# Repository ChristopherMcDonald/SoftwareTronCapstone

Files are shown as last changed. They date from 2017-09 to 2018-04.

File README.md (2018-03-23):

# SmartServe
An Autonomous Table Tennis Trainer

## Team Members
- Christopher McDonald
- Harit Patel
- Janak Patel
- Jared Rayner
- Nisarg Patel
- Sam Hamel
- Sharon Platkin

## Context
This project is the final capstone project for the Team Member's Bachelor of Engineering degrees.

## Overview
SmartServe is an autonomous table tennis training system for table tennis players with various skill levels. SmartServe aids in diagnosing and improving a player's performance over time. The system trains table tennis players by shooting table tennis balls towards the player and detects successful returns from the player. The system can further adapt to the player's weaknesses and help them overcome it through further training. Importantly, SmartServe alleviates the problems of finding and working with a coach for players, as well as coaches trying to train multiple players simultaneously. The system will be deemed a success if the table tennis players and coaches, can enjoy and see a value added by using SmartServe.

The project started at the beginning of the Fall 2017 academic term and will conclude at the end of the Winter 2018 term. In addition, the core project team consists of final year Software and Mechatronics Engineering students who are enrolled in the MECHTRON 4TB6/SFWRENG 4G06 capstone project course.

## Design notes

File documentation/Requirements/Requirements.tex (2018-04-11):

\documentclass[11pt]{article} 
\usepackage{geometry}
\geometry{letterpaper}

\usepackage{graphicx}   
\usepackage{amssymb}
\usepackage{float}
\usepackage{tabularx}
\usepackage{framed}
\usepackage{hyperref}
\hypersetup{
    colorlinks,
    citecolor=black,
    filecolor=black,
    linkcolor=black,
    urlcolor=black
}
\usepackage{cleveref}
%\usepackage[autostyle]{csquotes}
\usepackage[english]{babel}
\usepackage[backend=biber,style=numeric,sorting=none]{biblatex}
\addbibresource{cites.bib}

\defbibheading{bibliography}[\refname]{}

\begin{document}

\begin{titlepage}
	\newcommand{\HRule}{\rule{\linewidth}{0.2mm}}
	\begin{center}
	\textsc{\LARGE McMaster University}\\[1.5cm]
	
	\textsc{\Large SmartServe}\\[0.5cm]
	\textsc{\large Software \& Mechatronics Capstone}\\[0.5cm] 

	\HRule\\[0.4cm]
		{\huge\bfseries Requirements Document}\\[0.4cm]
	\HRule\\[0.4cm]
	
	\begin{minipage}[t][][t]{0.5\textwidth}
		\begin{flushleft} \large
			\emph{Authors:}\\
			Christopher McDonald - \textit{001312456} \\
			Harit Patel - \textit{001317372}\\
			Janak Patel - \textit{001307060} \\
			Jared Rayner - \textit{001311702}\\
			Nisarg Patel - \textit{001322805} \\
			Sam Hamel - \textit{001321692} \\
			Sharon Platkin - \textit{001316625} \\
		\end{flushleft}
	\end{minipage}
	~
	\begin{minipage}[t][][t]{0.4\textwidth}
		\begin{flushright} \large
			\emph{Professor:} \\
			Dr. Alan Wassyng \\[0.4cm]
			\emph{Teaching Assistants:} \\
			Bennett Mackenzie \\ 
			Nicholas Annable \\ 
			Stephen Wynn-Williams \\ 
			Viktor Smirnov
		\end{flushright}
	\end{minipage}\\[2cm]
	
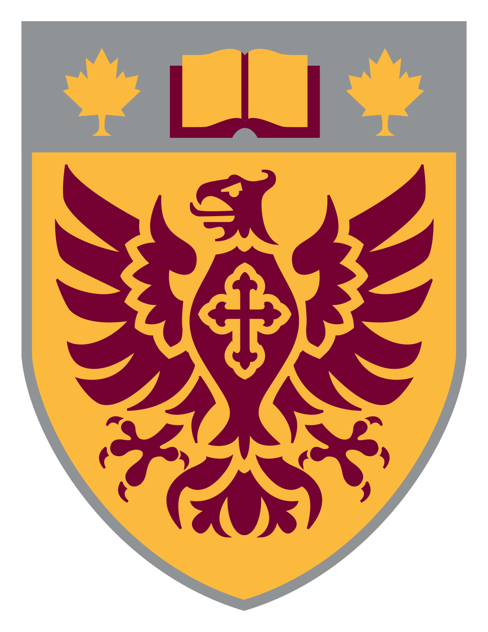
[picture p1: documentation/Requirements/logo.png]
	 \\
	{\large Last compiled on \today}
	\end{center}

\end{titlepage}

\tableofcontents
\listoffigures

\vfill
\begin{figure}[htbp]
   \centering
   \noindent\begin{tabularx}{\textwidth}{| >{\centering\arraybackslash}m{0.2\textwidth} | >{\centering\arraybackslash}m{0.2\textwidth} | >{\centering\arraybackslash}m{0.2\textwidth} | >{\centering\arraybackslash}m{0.285\textwidth} |}
   \hline 
   \textbf{Date} & \textbf{Revision} & \textbf{Comments} & \textbf{Author(s)} \\
   \hline
   10/06/2017 & 0 & Made Template, added sections and comments & Christopher McDonald \\ \hline
   10/13/2017 & 1 & Added Overview and reviewed & Christopher McDonald \& Sharon Platkin \\ \hline
   10/13/2017 & 2 & Reviewed and Corrected Project Drivers section & Nisarg Patel \\ \hline
   10/20/2017 & 3 & Functional Requirements & Christopher McDonald \& Sharon Platkin \\ 
\hline
   11/05/2017 & 4 & Final Revision and Review & Nisarg Patel 
  \& Christopher McDonald \\   \hline
   \end{tabularx}
   \caption{Revision History}
\end{figure}

\newpage

% TA Comments - Rev 1
%FIXED (see diagram in Appendix): What is a "4x4 grid"?
%FIXED (see accuracy added to fit crit for F2): Repeatability requirement on speed of ball? Angle of shooting mechanism or shot?
%FIXED (angular velocity is a function of speed by our design, and thus accuracy / repeatability would be the same added 5 degrees of error for degree): Add quantification of and a requirement on magnitude and repeatability of spin
%COMMENT by Janak: I think this requires a discussion. Magnitude of the spin is dependent on speed of the motor which might give us unrealistic spins at realistic speeds, will know with more testing. Going to need metrics for measuring spins also which could get challenging depending on how accurately we want to measure it.     
%FIXED (switched to 95): Detecting only 90% of returns may undermine the ability to train a person. Maybe aim for higher.
%COMMENT by Harit: Actually I thought 90% was quite reasonable to simply capture repeated mistakes and areas of improvement. Especially since SmartServe is catered to non-professional players
%COMMENY by Chris: fixed, good call ^
%COMMENT by Chris: yeah, I dunno. I just changed to appease him.
%IGNORED (will remove if it becomes necessary): Specific timeline isn't really needed for project overview. Might have to cut it in the future for extra space.
%FIXED (switched to 'Display'): Define ?Open Profile? from figure 8?
%??? (I don't know about this one, as per the Volere template cards it appears to be internal people, link here - http://www.volere.co.uk/pdf%20files/06%20Atomic%20Requirements.pdf): Originator of the requirements is not a specific team member, but rather of the defined stakeholders.
%COMMENT By Harit: I think he means the originator should be the stakeholder this requirement should be satisfied for. But I've never seen this before, should confirm with Alan. If change is needed, in most case it will be the player or the coach.
%COMMENT by Chris: good with asking Alan,
%FIXED (updated description): The system must be able to support 1000 users? - 1000 players? 1 player and 999 trainers? Make it less ambiguous.
%FIXED (removed requirement, did NOT update identifiers): The software for the system will execute on Linux, Windows and MacOS operating systems? - I thought the system was self contained, and as such it would be used with whatever embedded OS of your choosing. This seems to be more of a requirement for a standalone software package, not a self-contained system.
%IGNORED (I can defend it :P politics can be within customer organization, team's organization or country politicts, link here - https://www.utdallas.edu/~chung/SYSM6309/NFR-18-4-on-1.pdf): Requirement P1. How is this a political requirement? Seems to be a straightforward
%COMMENT by Harit: HAHA good shit!
%COMMENT by Janak: Requirement ID for Political Requirements and Performance requirements will both have a "P" suffix. Do the Req IDs have to be unique? 
%IGNORED (see above): Don?t try to dig for requirements, if you have no political requirements, put none. In fact, political requirements by itself is not a concept, not in context of engineering.

% NOTES: we will not be adjusting / refragging Requirement identifiers

\section{Introduction}
\subsection{Project Overview}
SmartServe is an autonomous table tennis training system for table tennis players with various skill levels. SmartServe aids in diagnosing and improving a player's performance over time. The system trains table tennis players by shooting table tennis balls towards the player and detects successful returns from the player. The system can further adapt to the player's weaknesses and help them overcome it through further training. Importantly, SmartServe alleviates the problems of finding and working with a coach for players, as well as coaches trying to train multiple players simultaneously. The system will be deemed a success if the table tennis players and coaches can enjoy and see value in using SmartServe.\\\\
The project started at the beginning of the Fall 2017 academic term and will conclude at the end of the Winter 2018 term. In addition, the core project team consists of final year Software and Mechatronics Engineering students who are enrolled in the MECHTRON 4TB6/SFWRENG 4G06 capstone project course.
\subsection{Naming Conventions and Terminology}
\label{sec:definitions}
The following terms and definitions will be used throughout this document:
\begin{itemize}
\item \textbf{System}: encompasses both the hardware and software parts of SmartServe
\item \textbf{Shooting Mechanism}: refers to the part of the system that shoots the table tennis balls towards the user side (player)
\item \textbf{Team}: all team members of the core capstone project, as noted in the list of Authors
\item \textbf{User Side}: the side of the table where the user (player) is standing
\item \textbf{System Side}: the side of the table where the electromechanical system is placed; it is the opposite side of the User Side
\item \textbf{ACID}: a database transaction which is atomic, consistent, isolated and durable
\item \textbf{FPS}: frames per second
\item \textbf{GUI}: graphical user interface
\item \textbf{Pitch}: rotation along the y-axis; this rotation angle primarily dictates the range of the ball from the net to the edge of the table on the user side
\item \textbf{Yaw}: rotation along the z-axis; this rotation angle primarily dictates the panning functionality of the shooting mechanism from the right side to the left side of the table
\item \textbf{Roll}: rotation along the x-axis
\end{itemize}
\begin{figure}[H]
   \centering
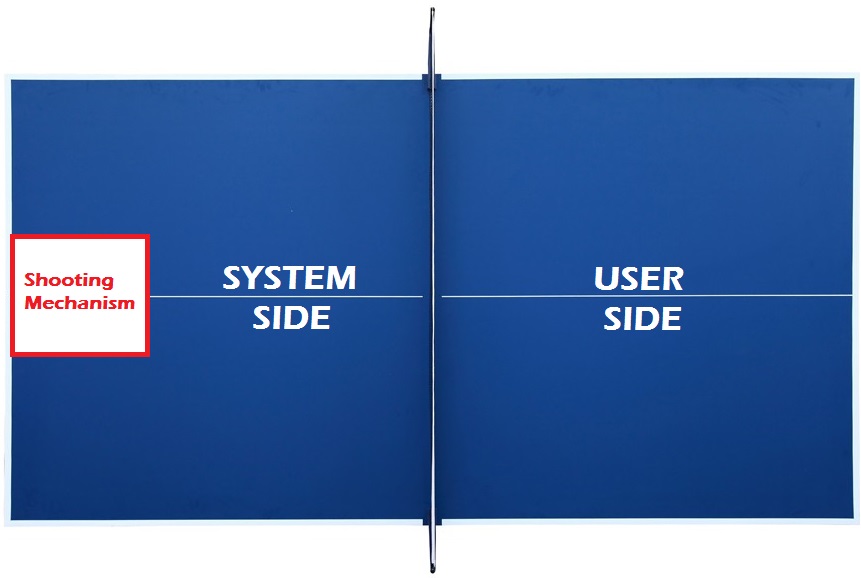
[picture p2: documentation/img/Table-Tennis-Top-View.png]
    %requires the graphicx package
   \caption{Top View of the Tennis Table}
   \label{fig:table-tennis-top-view}
\end{figure}
\begin{figure}[H]
   \centering
    %requires the graphicx package
   \caption{Pitch, Yaw and Roll Illustration}
   \label{fig:pitch_yaw_roll_diagram}
\end{figure}

\subsection{Relevant Facts \& Assumptions}
According to the International Table Tennis Federation (ITTF), the regulation table size is as follows: 2.74m long, 1.525m wide and 0.76m high off the ground. The table must be a uniformly dark colour with a 2cm-thick white line along the edge of the table, as well one running parallel to the 2.74m side in the middle of the table. The net in the middle of the table must be 15.25cm vertically high from the table~\autocite{ITTF}. A 3D representation of the table setup is illustrate in \Cref{fig:table-tennis-dim}. The size of a regulated table tennis ball is 40mm in diameter~\autocite{ITTF}. For this project, the \hyperref[sec:definitions]{team} will be using 40mm balls due to the ITTF regulation.\\
\begin{figure}[htbp]
   \centering
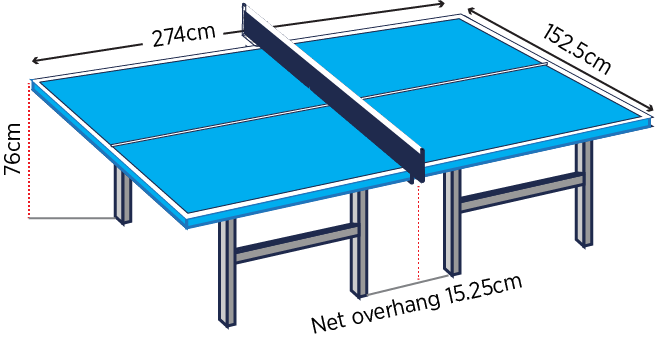
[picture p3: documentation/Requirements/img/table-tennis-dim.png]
    % requires the graphicx package
   \caption{3D Tennis Table with Dimensions}
   \label{fig:table-tennis-dim}
   % The Laws of Table Tennis. ITTF Handbook 2016. www.ittf.com/ittf_handbook/ittf_hb.html
\end{figure} \\
During gameplay, a valid serve must hit the \hyperref[sec:definitions]{server side} first, and then bounce once on the other player's side before being returned. After that is done, a valid return would be when the ball is hit by a player, after bouncing exactly once on their side, and bounces at least one time on the opposing player's side. If a serve touches the net and lands on the opposing player's side, it is a \textit{let}. No points are allocated and the turn must be re-served. These rules change during \textit{Double's Gameplay} but will not be considered for this project as only one user will be supported during operation.

\section{Project Drivers}
\subsection{Purpose}
% should include problem, lack of current solutions and ideal solution
When a player wants to improve their table tennis game, a typical solution is to hire a coach. However, this does not come without its challenges. Some of these challenges include scheduling, focusing on particular shots and receiving in-depth statistical feedback. Our proposed solution will consist of a shooting mechanism, a way to identify successful returns and a system to recommend different shots. Throughout the training session, the \hyperref[sec:definitions]{system} will provide the user with crucial feedback on the quality of their game. The system will consist of a electromechanical system to shoot the ball and a computer vision system to track the ball's location during flight. A server will also be added to store data, provide diagnostics and recommend shots given the user's past performance.
\subsection{Key Stakeholders}
\subsubsection{Client}
The client for this project comprises of the core development \hyperref[sec:definitions]{team} as both the idea and the project execution will be undertaken by the \hyperref[sec:definitions]{team}. It is also important to note that the project adviser, Dr. Alan Wassyng, as well as his teaching assistants will be involved in the project execution in order to provide guidance and critical feedback to the project \hyperref[sec:definitions]{team}.
\subsubsection{Users}
The primary users of this project are table tennis players. Our proposed \hyperref[sec:definitions]{system} will adapt to various playing styles and levels, and hence segmenting those players down further is not required at this stage. These users are more likely to play competitively, but could also play recreationally with friends or within a club focused around the sport. \\\\
The secondary users of this project are table tennis coaches. Although this \hyperref[sec:definitions]{system} could replace a coach, a coach could find value in using this system to aid in training and assisting multiple players at one time. The system will provide analytics on players performance that can be very useful when training someone over a long period of time.
\subsubsection{Faculty}
The Department of Computing and Software at McMaster University is also a key stakeholder for this project. The development \hyperref[sec:definitions]{team} are students of this department and would thus represent it through the work they perform. This project is also the amalgamation of the knowledge attained by the \hyperref[sec:definitions]{team} over their undergraduate degrees. If the project is unsuccessful, the department loses the opportunity to showcase it for future students and donors.

\section{Project Scope}
\subsection{The Scope of the Work and the Product}
In order to make the project feasible within the time constraint imposed on the \hyperref[sec:definitions]{team}, it will need to be scoped accordingly. One way we are scoping the project is by limiting the types of shots the \hyperref[sec:definitions]{system} can take. A return by the system would first contact the table on the \hyperref[sec:definitions]{\textit{User side}} where a serve would first contact the table on the \hyperref[sec:definitions]{\textit{System side}}. We are limiting the system to only preform returns. The system will make no attempt at returning any shots from the user. \\\\
After the user has returned a shot from the system, the system will not make any attempts to return a shot that is likely to be returned given the user's returns. This is to give the system the ability to focus on a particular type of shot the user is the least proficient at returning. The characteristics of the shot following any return will be determined by the system's mode and the proficiency of the player if available.
\subsubsection{Individual Product Use Cases}
The actors which will be interacting with the \hyperref[sec:definitions]{system} are the \textbf{trainee}, the \textbf{coach} and the \textbf{system administrator}. It is not necessary for a coach to be present, but they will have the ability to use the system alongside the trainee. See \Cref{fig:usecase} for the use case diagram. The following list contains all primary use cases:
\begin{itemize}
\item A trainee enters their login information
\item If the login information is correct, a trainee opens their training session on the \hyperref[sec:definitions]{system}
\item A trainee begins the training session
\item A trainee selects a training mode
\item A trainee pauses the training session
\item When the system is paused, a trainee ends the training session
\item A trainee inspects their performance
\end{itemize}
The following are secondary use cases:
\begin{itemize}
\item A coach inspects trainee's performance
\item A coach adjusts training parameters during training session
\item A system administrator calibrates the system for new tables of a non-regulation size
\end{itemize}

\begin{figure}[H]
   \centering
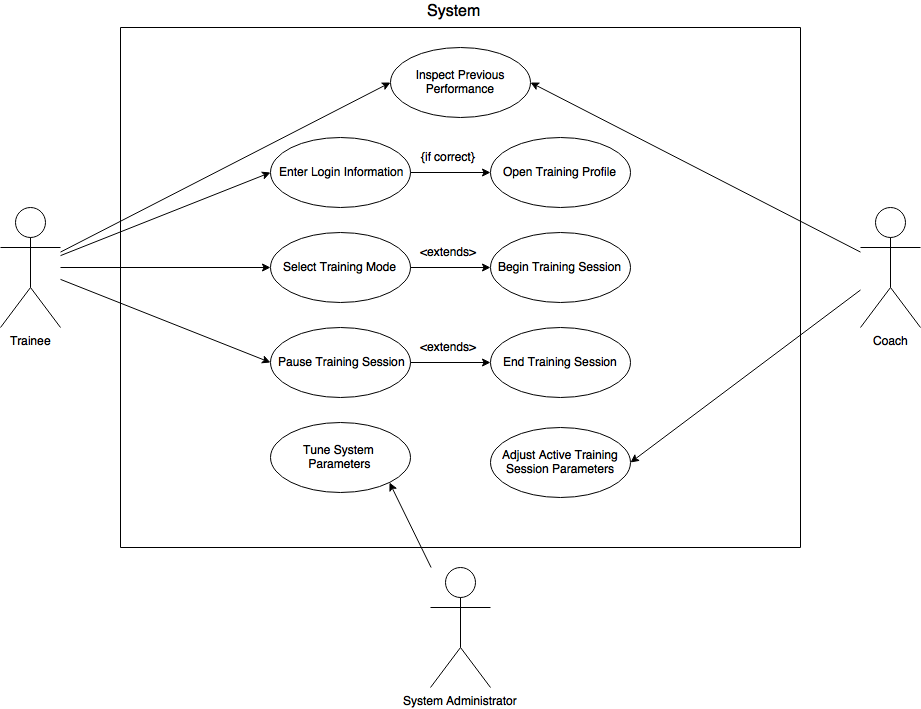
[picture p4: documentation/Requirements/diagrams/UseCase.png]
   
   \caption{Use Case Diagram}
   \label{fig:usecase}
\end{figure}
\subsection{Mandated Constraints}
The first constraint placed on the project is time. The deliverable and presentation dates have been set, concluding with the presentations booked for April 27, 2018. Therefore, the \hyperref[sec:definitions]{team} must successfully submit all of the deliverables and complete the project by April 27th, 2018. Additionally, a budget constraint of \$750 on the Bill of Materials (BOM) for the final product is also enforced.
\subsection{Undesired Behaviour} 
The shooting mechanism should not start, pause or end a session without the user triggering the event. The \hyperref[sec:definitions]{system} must also refrain from shooting the ball outside the speed and angle ranges specified. Furthermore, the system should not attempt to shoot balls when it runs out of balls. \\\\

\subsection{Variables}
\begin{figure}[H]
   \centering
   \noindent\begin{tabularx}{\textwidth}{| >{\centering\arraybackslash}m{0.2\textwidth} | >{\centering\arraybackslash}m{0.2\textwidth} | >{\centering\arraybackslash}m{0.2\textwidth} | >{\centering\arraybackslash}m{0.285\textwidth} |}
   \hline 
   \textbf{Variable Name} & \textbf{Type} & \textbf{Value} & \textbf{Description} \\ \hline
   \textit{Table Length} & Final & 274cm & The longest edge of the table tennis table \\ \hline
   \textit{Table Width} & Final & 152.5cm & Perpendicular to the \textit{Table Length} \\ \hline
   \textit{Ball Diameter} & Final & 40mm & Diameter of the ball used by the system \\ \hline
   \textit{Ball Location} & Monitored & X, Y and Z cm & Relative to the center of the table on its surface \\ \hline
   \textit{Shooting Mechanism Position} & Monitored & $\alpha_p$ and $\alpha_y$ degrees & Pitch and Yaw of the shooting mechanism \\ \hline
   \textit{User Performance} & Monitored & $\lambda_1$, $\lambda_2$, ... $\lambda_n$ & Return rates for n different shots from the user \\ \hline
 
\end{tabularx}
\caption{List of Variables}
\end{figure}

\subsection{Context Diagram}
\begin{figure}[H]
   \centering
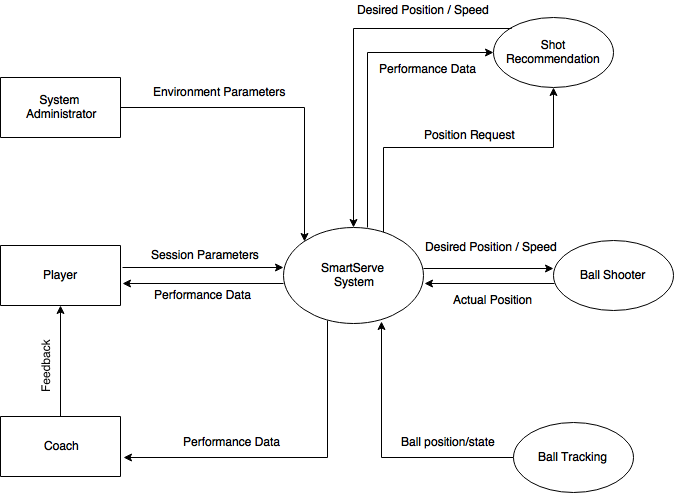
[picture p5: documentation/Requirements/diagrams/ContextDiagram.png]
   
   \caption{Context Diagram}
   \label{fig:ContextDiagram}
\end{figure}

\section{Functional Decomposition Diagram}
\begin{figure}[H]
   \centering
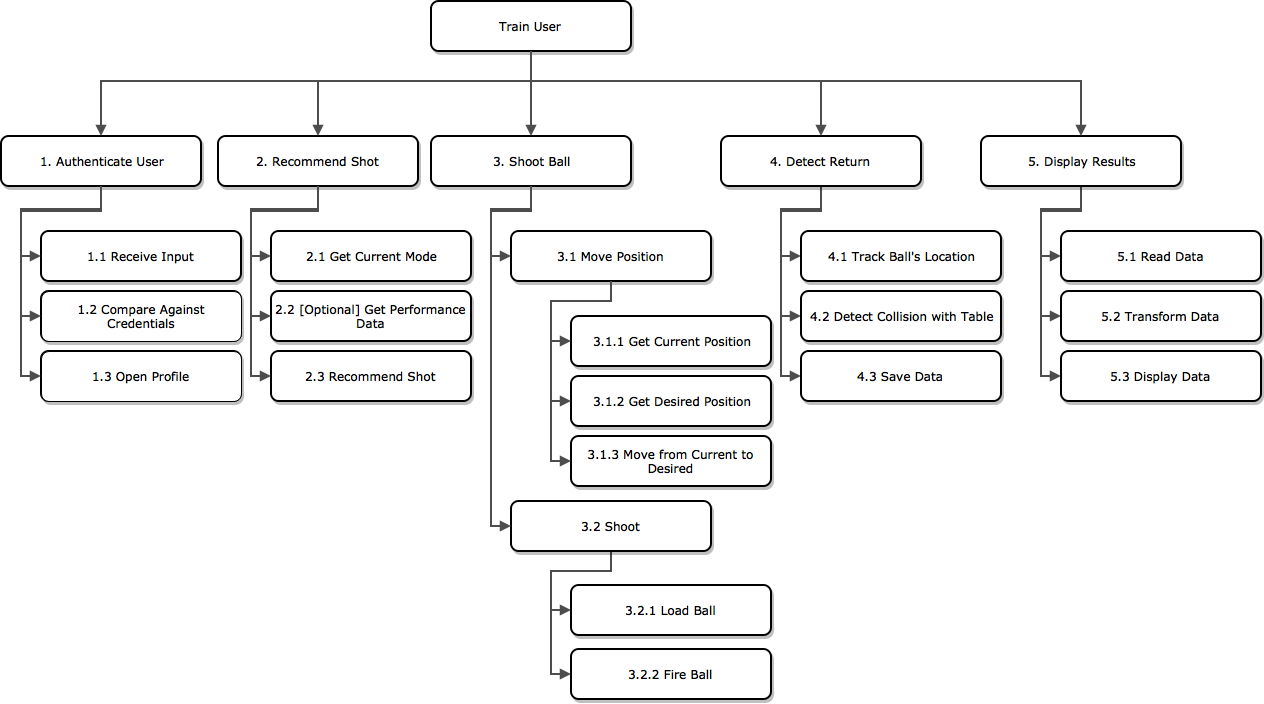
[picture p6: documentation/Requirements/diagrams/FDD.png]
   
   \caption{Functional Decomposition Diagram}
   \label{fig:fdd}
\end{figure}

\section{Functional Requirements}

\begin{framed}
	\noindent\textbf{Requirement ID}: F1 \hfill \textbf{Requirement Type}: F \hfill\\\\
	\noindent\textbf{Description}: The \hyperref[sec:definitions]{shooting mechanism} shoots the table tennis ball towards the \hyperref[sec:definitions]{user side} at various locations \\
	\textbf{Rationale}: Provides variability in the shots made towards the user \\
	\textbf{Fit Criterion}: The \hyperref[sec:definitions]{shooting mechanism} can hit a specified section of a 4x4 grid with an accuracy of 75\%, an example of this grid can be found in Figure \ref{fig:zones}\\\\
	\textbf{Originator}: Sharon Platkin \\\\
	\textbf{Priority}: High \hfill \\
	\noindent\textbf{History}: Created Oct. 20, 2017
\end{framed}

\begin{framed}
	\noindent\textbf{Requirement ID}: F2 \hfill \textbf{Requirement Type}: F \hfill\\\\
	\noindent\textbf{Description}: The \hyperref[sec:definitions]{shooting mechanism} shoots the table tennis ball towards the \hyperref[sec:definitions]{user side} at various speeds \\
	\textbf{Rationale}: Provides variability in the shots made towards the user \\
	\textbf{Fit Criterion}: Since the fastest recorded speed of a table tennis ball is 31.25 m/s, the system should be able to match at least half this speed~\autocite{thoughtco}. Specifically, the \hyperref[sec:definitions]{shooting mechanism} must shoot at speeds ranging from 10 to 15 m/s at discrete increments of 0.5 within 0.1 m/s of error \\\\
	\textbf{Originator}: Sharon Platkin \\\\
	\textbf{Priority}: High \hfill \\
	\noindent\textbf{History}: Created Oct. 20, 2017
\end{framed}

\begin{framed}
	\noindent\textbf{Requirement ID}: F3 \hfill \textbf{Requirement Type}: F \hfill\\\\
	\noindent\textbf{Description}: The \hyperref[sec:definitions]{shooting mechanism} shoots the table tennis ball towards the \hyperref[sec:definitions]{user side} at various degrees of \hyperref[sec:definitions]{Yaw} \\
	\textbf{Rationale}: Provides variability in the shots made towards the user \\
	\textbf{Fit Criterion}: The \hyperref[sec:definitions]{shooting mechanism} can shoot the ball at -30 to 30 degrees relative to the longest bisection of the table at discrete increments of 1 degree to have complete coverage of the \hyperref[sec:definitions]{User Side}, see \Cref{fig:calc} for calculations \\\\
	\textbf{Originator}: Sharon Platkin \\\\
	\textbf{Priority}: High \hfill \\
	\noindent\textbf{History}: Created Oct. 20, 2017
\end{framed}

\begin{framed}
	\noindent\textbf{Requirement ID}: F4 \hfill \textbf{Requirement Type}: F \hfill\\\\
	\noindent\textbf{Description}: The \hyperref[sec:definitions]{shooting mechanism} shoots the table tennis ball towards the \hyperref[sec:definitions]{user side} of the table with various degrees of roll \\
	\textbf{Rationale}: Provides variability in the shots made towards the user \\
	\textbf{Fit Criterion}: The \hyperref[sec:definitions]{shooting mechanism} can spin the ball at 0 to 360 degrees in discrete increments of 45 degrees on the longitudinal axis with 5 degrees of error\\\\ % longitudinal - refers to lengthwise as opposed to across
	\textbf{Originator}: Sharon Platkin \\\\
	\textbf{Priority}: High \hfill \\
	\noindent\textbf{History}: Created Oct. 20, 2017
\end{framed}

\begin{framed}
	\noindent\textbf{Requirement ID}: F5 \hfill \textbf{Requirement Type}: F \hfill\\\\
	\noindent\textbf{Description}: The \hyperref[sec:definitions]{system} can detect a successful return by the user \\
	\textbf{Rationale}: Allows quantitative information to be collected on the user's performance \\
	\textbf{Fit Criterion}: The system must detect 90\% of all successful returns made by the user\\\\
	\textbf{Originator}: Sharon Platkin \\\\
	\textbf{Priority}: High \hfill \\
	\noindent\textbf{History}: Created Oct. 20, 2017
\end{framed}

\begin{framed}
	\noindent\textbf{Requirement ID}: F6 \hfill \textbf{Requirement Type}: F \hfill\\\\
	\noindent\textbf{Description}: The \hyperref[sec:definitions]{system} saves the details for each shot taken by the shooting mechanism \\
	\textbf{Rationale}: Serves the purpose of saving the state and resuming sessions over time \\
	\textbf{Fit Criterion}: After each shot is returned, an \hyperref[sec:definitions]{ACID} save transaction is performed \\\\
	\textbf{Originator}: Christopher McDonald \\\\
	\textbf{Priority}: Medium \hfill \\
	\noindent\textbf{History}: Created Oct. 20, 2017
\end{framed}

\begin{framed}
	\noindent\textbf{Requirement ID}: F7 \hfill \textbf{Requirement Type}: F \hfill\\\\
	\noindent\textbf{Description}: The \hyperref[sec:definitions]{system} can load a previously saved state \\
	\textbf{Rationale}: This will allow the user to continue a training session at different times, even if the system is powered down \\
	\textbf{Fit Criterion}: \\\\
	\textbf{Originator}: Christopher McDonald \\\\
	\textbf{Priority}: Medium \hfill \\
	\noindent\textbf{History}: Created Oct. 20, 2017
\end{framed}

\begin{framed}
	\noindent\textbf{Requirement ID}: F8 \hfill \textbf{Requirement Type}: F \hfill\\\\
	\noindent\textbf{Description}: The \hyperref[sec:definitions]{system} allows the creation of a new user \\
	\textbf{Rationale}: This allows many users to use one system \\
	\textbf{Fit Criterion}: A user must be able to be created only if the user does not already exist in the system \\\\
	\textbf{Originator}: Christopher McDonald \\\\
	\textbf{Priority}: Medium \hfill \\
	\noindent\textbf{History}: Created Oct. 20, 2017
\end{framed}

\begin{framed}
	\noindent\textbf{Requirement ID}: F9 \hfill \textbf{Requirement Type}: F \hfill\\\\
	\noindent\textbf{Description}: The \hyperref[sec:definitions]{system} must authenticate users \\
	\textbf{Rationale}: This will ensure a user can access their profile and restrict other users from accessing their profile \\
	\textbf{Fit Criterion}: No user can access another user's profile and will have access to their own 99\% of the time \\\\
	\textbf{Originator}: Christopher McDonald \\\\
	\textbf{Priority}: High \hfill \\
	\noindent\textbf{History}: Created Oct. 20, 2017
\end{framed}

\begin{framed}
	\noindent\textbf{Requirement ID}: F10 \hfill \textbf{Requirement Type}: F \hfill\\\\
	\noindent\textbf{Description}: The \hyperref[sec:definitions]{system} can pause the shooting mechanism \\
	\textbf{Rationale}: A user may need to attend other matters during training or get real-time feedback from the system \\
	\textbf{Fit Criterion}: After instantiating the pause process, the system shoots at most 1 more ball(s) \\\\
	\textbf{Originator}: Christopher McDonald \\\\
	\textbf{Priority}: High \hfill \\
	\noindent\textbf{History}: Created Oct. 20, 2017
\end{framed}

\begin{framed}
	\noindent\textbf{Requirement ID}: F11 \hfill \textbf{Requirement Type}: F \hfill\\\\
	\noindent\textbf{Description}: The \hyperref[sec:definitions]{system} can end the training session \\
	\textbf{Rationale}: This will be used when a user is done training \\
	\textbf{Fit Criterion}: N/A \\\\
	\textbf{Originator}: Christopher McDonald \\\\
	\textbf{Priority}: High \hfill \\
	\noindent\textbf{History}: Created Oct. 20, 2017
\end{framed}

\begin{framed}
	\noindent\textbf{Requirement ID}: F12 \hfill \textbf{Requirement Type}: F \hfill\\\\
	\noindent\textbf{Description}: The \hyperref[sec:definitions]{system} can resume a training session from a paused state \\
	\textbf{Rationale}: N/A \\
	\textbf{Fit Criterion}: N/A \\\\
	\textbf{Originator}: Christopher McDonald \\\\
	\textbf{Priority}: High \hfill \\
	\noindent\textbf{History}: Created Oct. 20, 2017
\end{framed}

\begin{framed}
	\noindent\textbf{Requirement ID}: F13 \hfill \textbf{Requirement Type}: F \hfill\\\\
	\noindent\textbf{Description}: The \hyperref[sec:definitions]{system} can display the user's performance over a custom time range \\
	\textbf{Rationale}: This will aid the user in diagnosing their ability to play table tennis \\
	\textbf{Fit Criterion}: N/A\\\\
	\textbf{Originator}: Christopher McDonald \\\\
	\textbf{Priority}: High \hfill \\
	\noindent\textbf{History}: Created Oct. 20, 2017
\end{framed}

\begin{framed}
	\noindent\textbf{Requirement ID}: F14 \hfill \textbf{Requirement Type}: F \hfill\\\\
	\noindent\textbf{Description}: The \hyperref[sec:definitions]{system} has a \textbf{training} mode \\
	\textbf{Rationale}: This mode will focus on playing to the user's weaknesses more so than others \\
	\textbf{Fit Criterion}: After 100 pseudo-randomly distributed shots, the system will begin to distribute the shots differently. By ordering each class of shot from the least to most returned, the first 15\%, the next 35\% and the last half will all receive an equal share of shots. \\\\
	\textbf{Originator}: Christopher McDonald \\\\
	\textbf{Priority}: High \hfill \\
	\noindent\textbf{History}: Created Oct. 20, 2017
\end{framed}

\begin{framed}
	\noindent\textbf{Requirement ID}: F15 \hfill \textbf{Requirement Type}: F \hfill\\\\
	\noindent\textbf{Description}: The \hyperref[sec:definitions]{system} has a \textbf{one-shot} mode \\
	\textbf{Rationale}: This mode will focus on playing to one particular class of shot, as described by the user \\
	\textbf{Fit Criterion}: For all shots performed in this mode, 90\% must be classified as the same as the one entered \\\\
	\textbf{Originator}: Christopher McDonald \\\\
	\textbf{Priority}: Medium \hfill \\
	\noindent\textbf{History}: Created Oct. 20, 2017
\end{framed}

\begin{framed}
	\noindent\textbf{Requirement ID}: F16 \hfill \textbf{Requirement Type}: F \hfill\\\\
	\noindent\textbf{Description}: The \hyperref[sec:definitions]{system} allows a user to adjust training parameters during a session which is active or paused \\
	\textbf{Rationale}: A coach may want to push a player to train in a particular area \\
	\textbf{Fit Criterion}:  \\\\
	\textbf{Originator}: Christopher McDonald \\\\
	\textbf{Priority}: Low \hfill \\
	\noindent\textbf{History}: Created Oct. 20, 2017
\end{framed}

\begin{framed}
	\noindent\textbf{Requirement ID}: F17 \hfill \textbf{Requirement Type}: F \hfill\\\\
	\noindent\textbf{Description}: The \hyperref[sec:definitions]{system} can be calibrated for the size of the table \\
	\textbf{Rationale}: As performed by a system administrator, it should be usable for all non-regulation table sizes \\
	\textbf{Fit Criterion}: The system follows all documented requirements \\\\
	\textbf{Originator}: Christopher McDonald \\\\
	\textbf{Priority}: High \hfill \\
	\noindent\textbf{History}: Created Oct. 20, 2017
\end{framed}

\begin{framed}
	\noindent\textbf{Requirement ID}: F18 \hfill \textbf{Requirement Type}: F \hfill\\\\
	\noindent\textbf{Description}: The \hyperref[sec:definitions]{shooting mechanism} will shoot a ball once the previous has been returned to the \hyperref[sec:definitions]{system side} or 1.5 seconds after the previous shot, whichever happens first\\
	\textbf{Rationale}: This will ensure the system is reasonably fast and keeps the user engaged, as well as compensates for more experienced players. \\
	\textbf{Fit Criterion}: N/A \\\\
	\textbf{Originator}: Christopher McDonald \\\\
	\textbf{Priority}: High \hfill \\
	\noindent\textbf{History}: Created Oct. 20, 2017
\end{framed}

\section{Non-Functional Requirements}

\subsection{Look and Feel Requirements}
\begin{framed}
	\noindent\textbf{Requirement ID}: LF1 \hfill\\\\
	\noindent\textbf{Description}: The \hyperref[sec:definitions]{system} will have a minimalist design that is easy to navigate through \\
	\textbf{Rationale}: A minimalistic design will help with user discover all the options and settings of the system  \\
	\textbf{Fit Criterion}: The user must be able to navigate to any feature from the profile page in at most two steps.  \\\\
	\textbf{Originator}: Sam Hamel \\\\
	\textbf{Priority}: Medium \hfill \\
	\noindent\textbf{History}: Created Oct. 27, 2017
\end{framed}

\subsection{Usability and Humanity Requirements}
\begin{framed}
	\noindent\textbf{Requirement ID}: UH1 \hfill\\\\
	\noindent\textbf{Description}: The \hyperref[sec:definitions]{system} must be intuitive to use \\
	\textbf{Rationale}: As the system is adding onto an existing process, it should not cause strain for the user to operate \\
	\textbf{Fit Criterion}: The user must be able to create a user in less than 30 seconds. The user must be able to initiate \textit{one-shot} mode in less than 2 minutes from opening their profile.  \\\\
	\textbf{Originator}: Christopher McDonald \\\\
	\textbf{Priority}: High \hfill \\
	\noindent\textbf{History}: Created Oct. 20, 2017
\end{framed}

\begin{framed}
	\noindent\textbf{Requirement ID}: UH2 \hfill\\\\
	\noindent\textbf{Description}: The \hyperref[sec:definitions]{system} will operate using the English language \\
	\textbf{Rationale}: Some of the Development \hyperref[sec:definitions]{team} only speaks English \\
	\textbf{Fit Criterion}: All outputs generated by the system will be in English  \\\\
	\textbf{Originator}: Sharon Platkin \\\\
	\textbf{Priority}: High \hfill \\
	\noindent\textbf{History}: Created Oct. 27, 2017
\end{framed}

\subsection{Performance Requirements}

\begin{framed}
	\noindent\textbf{Requirement ID}: P1 \hfill\\\\
	\noindent\textbf{Description}: The response time of feedback for user input must be less than or equal to 100ms \\
	\textbf{Rationale}: 100ms is the approximate maximum amount of time for the user to perceive the system as reacting instantaneously~\autocite{response}. Users should feel that all inputs have been registered by the system\\
	\textbf{Fit Criterion}: Any click inputs that generate feedback must do so in at most 100ms.  \\\\
	\textbf{Originator}: Sam Hamel \\\\
	\textbf{Priority}: High \hfill \\
	\noindent\textbf{History}: Created Oct. 27, 2017
\end{framed}

\begin{framed}
	\noindent\textbf{Requirement ID}: P2 \hfill\\\\
	\noindent\textbf{Description}: The system must include all but the previous 3 shots made toward the user  \\
	\textbf{Rationale}: This will keep the performance measures relatively up to date for relevant and up-to-date feedback \\
	\textbf{Fit Criterion}: Any results by any return from the player must be displayed on the \hyperref[sec:definitions]{GUI} (graphical user interface) before the player returns 3 more shots \\\\
	\textbf{Originator}: Sam Hamel \\\\
	\textbf{Priority}: High \hfill \\
	\noindent\textbf{History}: Created Oct. 27, 2017
\end{framed}

\begin{framed}
	\noindent\textbf{Requirement ID}: P4 \hfill\\\\
	\noindent\textbf{Description}: The \hyperref[sec:definitions]{system} must be able to support a total of 1000 users, consisting of players and coaches \\
	\textbf{Rationale}: If the system is used by a company, they will have a large amount of users using the system\\
	\textbf{Fit Criterion}: The system can store up to a thousand user profiles and their accompanying performance history data \\\\
	\textbf{Originator}: Sam Hamel \\\\
	\textbf{Priority}: Medium \hfill \\
	\noindent\textbf{History}: Created Oct. 27, 2017
\end{framed}

\begin{framed}
	\noindent\textbf{Requirement ID}: P5 \\\\
	\noindent\textbf{Description}: The \hyperref[sec:definitions]{system} will be able to support only one user playing at any given time \\
	\textbf{Rationale}: The system will not be able to differentiate between player returns if they were more than one user playing at the same time \\
	\textbf{Fit Criterion}: The system will work as expected for one player playing 99\% of the time \\\\
	\textbf{Originator}: Sam Hamel \\\\
	\textbf{Priority}: High \hfill \\
	\noindent\textbf{History}: Created Oct. 27, 2017
\end{framed}

\subsection{Operational and Environmental Requirements}

\begin{framed}
	\noindent\textbf{Requirement ID}: OE2 \\\\
	\noindent\textbf{Description}: The \hyperref[sec:definitions]{system} will be functional in indoor settings with bright florescent lighting in the room \\
	\textbf{Originator}: Sam Hamel \\\\
	\textbf{Priority}: High \hfill \\
	\noindent\textbf{History}: Created Oct. 27, 2017
\end{framed}

\subsection{Maintainability and Support Requirements}

\begin{framed}
	\noindent\textbf{Requirement ID}: MS2 \\\\
	\noindent\textbf{Description}: The \hyperref[sec:definitions]{system} should be able to add new metrics to analyze performance\\
	\textbf{Rationale}: More efficient and appropriate methods may be found in order to analyze player performance\\
	\textbf{Fit Criterion}: The system will be able to add new performance metrics and analysis methods so long as no changes need to be made to the hardware\\\\
	\textbf{Originator}: Sam Hamel \\\\
	\textbf{Priority}: High \hfill \\
	\noindent\textbf{History}: Created Oct. 27, 2017
\end{framed}

\subsection{Security Requirements}
\begin{framed}
	\noindent\textbf{Requirement ID}: S1 \hfill\\\\
	\noindent\textbf{Description}: The \hyperref[sec:definitions]{system} must hash all passwords for user profiles \\
	\textbf{Rationale}: If the system is compromised, no person should be able to read user's passwords in plain text. \\
	\textbf{Fit Criterion}: The system uses a hashing algorithm currently supported by NIST, the National Institute of Standards and Technology.\\\\
	\textbf{Originator}: Christopher McDonald \\\\
	\textbf{Priority}: High \hfill \\
	\noindent\textbf{History}: Created Oct. 20, 2017
\end{framed}

\begin{framed}
	\noindent\textbf{Requirement ID}: S2 \hfill\\\\
	\noindent\textbf{Description}: The \hyperref[sec:definitions]{system} must encrypt all performance data for each user \\
	\textbf{Rationale}: If the system is compromised, no person should be able to exploit an opponent's weaker aspects \\
	\textbf{Fit Criterion}: The system uses an encrypting algorithm currently supported by NIST, the National Institute of Standards and Technology.\\\\
	\textbf{Originator}: Christopher McDonald \\\\
	\textbf{Priority}: Low \hfill \\
	\noindent\textbf{History}: Created Oct. 20, 2017
\end{framed}

\subsection{Political Requirements}
\begin{framed}
	\noindent\textbf{Requirement ID}: P1\\\\
	\noindent\textbf{Description}: The \hyperref[sec:definitions]{system} must allow full read access for coaches \\
	\textbf{Rationale}: If a coach purchases this system, they should be able to analyze all players information for training purposes \\
	\textbf{Fit Criterion}: \\\\
	\textbf{Originator}: Christopher McDonald \\\\
	\textbf{Priority}: Medium \hfill \\
	\noindent\textbf{History}: Created Oct. 20, 2017
\end{framed}
\subsection{Legal \& Compliance Requirements}
\begin{framed}
	\noindent\textbf{Requirement ID}: LC1 \hfill\\\\
	\noindent\textbf{Description}: The \hyperref[sec:definitions]{system} must comply and operate for all ITTF rules and regulations \\
	\textbf{Rationale}: ITTF mandates the acceptance of all table tennis equipment and the system should work with these to be used by professional players \\
	\textbf{Fit Criterion}: The system must work for any 2 tables and nets which the ITTF has accepted \\\\
	\textbf{Originator}: Christopher McDonald \\\\
	\textbf{Priority}: High \hfill \\
	\noindent\textbf{History}: Created Oct. 20, 2017
\end{framed}
\subsection{Health and Safety Requirements}
\begin{framed}
	\noindent\textbf{Requirement ID}: HS1 \hfill\\\\
	\noindent\textbf{Description}: The \hyperref[sec:definitions]{shooting mechanism} will always hit the table at least once  \\
	\textbf{Rationale}: This will give the user more time and context to react to the shot \\
	\textbf{Fit Criterion}: The system imposes limits for speed and pitch of the shot \\\\
	\textbf{Originator}: Christopher McDonald \\\\
	\textbf{Priority}: High \hfill \\
	\noindent\textbf{History}: Created Oct. 20, 2017
\end{framed}

\begin{framed}
	\noindent\textbf{Requirement ID}: HS2 \hfill\\\\
	\noindent\textbf{Description}: The \hyperref[sec:definitions]{shooting mechanism} will not shoot the ball faster than 22 m/s \\
	\textbf{Rationale}: This is 70\% of one of the world's fastest shots taken in table tennis and is unlikely to be of any practical use\\
	\textbf{Fit Criterion}: The system will constrain the speed of its shooting mechanism \\\\
	\textbf{Originator}: Christopher McDonald \\\\
	\textbf{Priority}: High \hfill \\
	\noindent\textbf{History}: Created Oct. 20, 2017
\end{framed}

\begin{framed}
	\noindent\textbf{Requirement ID}: HS3 \hfill\\\\
	\noindent\textbf{Description}: The \hyperref[sec:definitions]{system} should have no exposed electronic wiring or components \\
	\textbf{Rationale}: This will protect the user from electric shocks and the system from damage \\
	\textbf{Fit Criterion}: Only by disassembling the system should wiring and components be exposed \\\\
	\textbf{Originator}: Christopher McDonald \\\\
	\textbf{Priority}: High \hfill \\
	\noindent\textbf{History}: Created Oct. 28, 2017
\end{framed}

\begin{framed}
	\noindent\textbf{Requirement ID}: HS4 \hfill\\\\
	\noindent\textbf{Description}: The \hyperref[sec:definitions]{system} will carry warnings around moving parts  \\
	\textbf{Rationale}: Moving parts can expose users to risk of pinching extremities \\
	\textbf{Fit Criterion}: Warning signs are displayed at every point of risk \\\\
	\textbf{Originator}: Christopher McDonald \\\\
	\textbf{Priority}: High \hfill \\
	\noindent\textbf{History}: Created Oct. 28, 2017
\end{framed}

\begin{framed}
	\noindent\textbf{Requirement ID}: HS5 \hfill\\\\
	\noindent\textbf{Description}: The \hyperref[sec:definitions]{system} will have a button to cease all power to the system \\
	\textbf{Rationale}: In the case of dangerous operation, the system must be able to be powered off manually \\
	\textbf{Fit Criterion}: One button will shut down system and is labeled as such \\\\
	\textbf{Originator}: Christopher McDonald \\\\
	\textbf{Priority}: High \hfill \\
	\noindent\textbf{History}: Created Oct. 28, 2017
\end{framed}

\section{Project Issues}
\subsection{Open Issues}
Due to the nature of the project, all aspects of it must operate proficiently in order for it to be successful. For example, one potential issue would arise if no spin must be applied to the ball. Without detailing how the system works, the team considers this to be difficult without hardware that has no error in operation. \\\\
Some players may be able to hit the ball much faster than the solution we build to capture successful returns. For example, if some optical sensor is used it must be fast enough to capture the ball at the point of contact, or very close to it, in order to accurately determine if it did hit the table. \\\\
Between shots of the \hyperref[sec:definitions]{system}, it must determine where the next shot will be, get into the necessary position and shoot the ball. For some cases, the shot determination could take longer than usual or the distance between initial and final state could be far. This could jeopardize the system's ability to meet requirement F18.
\subsection{Off-the-Shelf Solutions}
For the second issue noted in the above section, a high speed camera could be used but would exceed the budget constraint placed on this project. For example, a GoPro HERO5 camera can film at 120fps but costs \$490~\autocite{amazon-gopro}.
Additionally, a camera which can film up to 500fps costs as much as \$999.99~\autocite{all-sport}.
These would far constrain our budget, but would solve the issue should it arise. An alternative could be mat embedded with sensors, omitting all optical sensor requirements. A mat which is roughly one-quarter the size of what we would need to cover one side of table costs \$119.99, which includes a wireless pager and any markup costs done by the manufacturer. A total estimate for our materials can be estimated to be \$150.00.\\\\
For the third issue, faster motors could be used to make the shooting mechanism move faster. However, these also must fit in the budget and will be adjusted accordingly to do so.
\subsection{New Problems}
As of \today, no new problems exist.
\subsection{Risks}
The largest and only risk to note is potentially going over budget. This is mainly with respect to the proficiency of the sensors and motors used as it is typically positively correlated with price. 
\subsection{User Documentation \& Training}
The user should be informed on the following items in order to use the system effectively:
\begin{itemize}
\item Available training modes and their purpose
\item How to read performance charts and data
\item Load table tennis balls into the correct location
\item Ensure system is positioned correctly
\end{itemize}
\section{Likely Changes}
As noted in the Project Goals document, many of the anticipated changes include enhanced accuracy of some requirements. These include the following:
\begin{itemize}
\item F1 will be changed to a 8x8 grid and then a 16x16 grid
\item Adding a \textbf{random} shooting mode
\item Adding variable heights for the shooting mechanism
\item Adding the ability to track the ball throughout its travel across the table
\end{itemize}
\section{Appendix}
\begin{figure}[H]
\centering

\caption{Valid Range of Shot Calculation}
\label{fig:calc}
\end{figure}

\begin{figure}[H]
   \centering
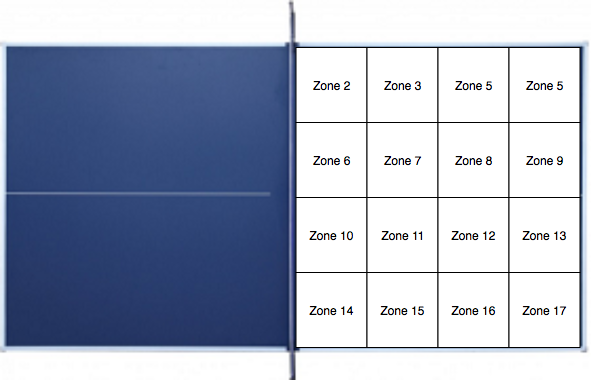
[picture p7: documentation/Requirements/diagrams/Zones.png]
    % requires the graphicx package
   \caption{Table Tennis Table with 4x4 Grid Zones}
   \label{fig:zones}
\end{figure}
\section{References}
\printbibliography
\end{document}

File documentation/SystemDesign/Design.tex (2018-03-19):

\documentclass[11pt]{article}
\usepackage{geometry}
\geometry{letterpaper}

\usepackage{graphicx}
\usepackage{amssymb}
\usepackage{float}
\usepackage{tabularx}
\usepackage{multicol}
\usepackage{rotating}
\usepackage{hyperref}
\hypersetup{
    colorlinks,
    citecolor=black,
    filecolor=blue,
    linkcolor=black,
    urlcolor=black
}

% TODOs:
% ask Nick about lines in Seq Diagram, ask Nick about need 3D model, ask Nick about entering project goals
% switch to cleveref

\begin{document}

\begin{titlepage}
	\newcommand{\HRule}{\rule{\linewidth}{0.2mm}}
	\begin{center}
	\textsc{\LARGE McMaster University}\\[1.5cm]

	\textsc{\Large SmartServe}\\[0.5cm]
	\textsc{\large Software \& Mechatronics Capstone}\\[0.5cm]

	\HRule\\[0.4cm]
		{\huge\bfseries High Level System Design}\\[0.4cm]
	\HRule\\[0.4cm]

	\begin{minipage}[t][][t]{0.5\textwidth}
		\begin{flushleft} \large
			\emph{Authors:}\\
			Christopher McDonald - \textit{001312456} \\
			Harit Patel - \textit{001317372}\\
			Janak Patel - \textit{001307060} \\
			Jared Rayner - \textit{001311702}\\
			Nisarg Patel - \textit{001322805} \\
			Sam Hamel - \textit{001321692} \\
			Sharon Platkin - \textit{001316625} \\
		\end{flushleft}
	\end{minipage}
	~
	\begin{minipage}[t][][t]{0.4\textwidth}
		\begin{flushright} \large
			\emph{Professor:} \\
			Dr. Alan Wassyng \\[0.4cm]
			\emph{Teaching Assistants:} \\
			Bennett Mackenzie \\
			Nicholas Annable \\
			Stephen Wynn-Williams \\
			Viktor Smirnov
		\end{flushright}
	\end{minipage}\\[2cm]

	 \\
	{\large Last compiled on \today}
	\end{center}

\end{titlepage}

\tableofcontents
\listoffigures

\vfill
\begin{figure}[H]
   \centering
   \noindent\begin{tabularx}{\textwidth}{| >{\centering\arraybackslash}m{0.2\textwidth} | >{\centering\arraybackslash}m{0.2\textwidth} | >{\centering\arraybackslash}m{0.2\textwidth} | >{\centering\arraybackslash}m{0.285\textwidth} |}
   \hline
   \textbf{Date} & \textbf{Revision} & \textbf{Comments} & \textbf{Author(s)} \\ \hline
   Dec 1, 2017 & 1.0 & Main content done for all sections & Christopher McDonald \\ \hline
   Dec 13, 2017 & 1.1 & Corrected Document Overview & Nisarg Patel \\ \hline
   Dec 14, 2017 & 1.2 & Refined Project Scope \& System Description (Section 2) & Nisarg Patel \\ \hline
   Dec 17, 2017 & 1.3 & Added CRC card intro and reviewed & Christopher McDonald \\ \hline
   Dec 21, 2017 & 1.4 & Edited entire document & Sharon Platkin \\ \hline
   Dec 21, 2017 & 1.5 & Added Arduino Diagrams and Shooter Information & Nisarg Patel \\ \hline	
   Mar 9, 2018 & 2.0 & Added Likely / Unlikely Changes and Assumptions, Removed Shot Optimizer & Christopher McDonald \\ \hline	
   Mar 9, 2018 & 2.1 & Added motor specifications & Janak Patel \\ \hline	
   Mar 10, 2018 & 2.2 & Added details on CV and SR, fixed Start Sequence Diagram & Christopher McDonald \\ \hline
   Mar 10, 2018 & 2.3 & Fixed CRC cards for changes to requirements & Christopher McDonald \\ \hline
   Mar 18, 2018 & 2.4 & Converted to overall design, added in low level / component details & Christopher McDonald \\ \hline
   \end{tabularx}
   \caption{Revision History}
\end{figure}
\newpage
\section{Introduction}
\subsection{Project Overview}
SmartServe is an autonomous table tennis training system for table tennis players with various skill levels. SmartServe aids in diagnosing and improving a player's performance over time. The system trains table tennis players by shooting table tennis balls towards the player and detects successful returns from the player. The system can further adapt to the player's weaknesses and help them overcome it through further training. Importantly, SmartServe alleviates the problems of finding and working with a coach for players, as well as coaches trying to train multiple players simultaneously. The system will be deemed a success if the table tennis players and coaches can enjoy and see some value added by using SmartServe.\\\\
The project started at the beginning of the Fall 2017 academic term and will conclude at the end of the Winter 2018 term. In addition, the core project team consists of final year Software and Mechatronics Engineering students who are enrolled in the MECHTRON 4TB6/SFWRENG 4G06 capstone project course.
\subsection{Document Overview}
The purpose of this document is to provide an overview of the system design which meets the system requirements as specified in the \href{run:../Requirements/Requirements.pdf}{Requirements Document}. The system will be decomposed into subsystems, where each has responsibilities and is designed to fulfill certain requirements. The subsystems will have their intended input, expected output and description of how the module will be used. In further documentation, each will be designed in a way which is abstracted from this document's perspective. The expected use cases will also be detailed to understand the expectations of the user and how each subsystem interacts with one another. A more detailed view of this including timing as a factor will be detailed in the Sequence Diagram section. \\ \\ % TODO LINK EVERYTHING
For each subsystem, its purpose will be defined with respect to the overall system. After doing so, detailed input and output parameters will be defined. How each subsystem is architected is out of scope for this document and will be defined in further documentation. \\ \\

\subsection{Naming Conventions and Terminology}
\label{sec:definitions}
The following terms and definitions will be used throughout this document:
\begin{itemize}
% Alphabetical order is highly preferred as it eases user navigation
\item \textbf{ACID}: a database transaction which is atomic, consistent, isolated and durable
\item \textbf{CV}: computer vision
\item \textbf{FPS}: frames per second
\item \textbf{FSM}: finite state machine, shows transitions between states
\item \textbf{GUI}: graphical user interface
\item \textbf{IPO}: input process output
\item \textbf{Pitch}: rotation along the y-axis; this rotation angle primarily dictates the range of the ball from the net to the edge of the table on the user side
\item \textbf{Roll}: rotation along the x-axis
\item \textbf{Shooting Mechanism}: refers to the part of the system that shoots the table tennis balls towards the user side (player) Please refer to Figure \ref{fig:table-tennis-top-view} for visual illustration
\item \textbf{System}: encompasses both the hardware and software parts of SmartServe
\item \textbf{System Side}: the side of the table where the electromechanical system is placed; it is the opposite side of the User Side Please refer to Figure \ref{fig:table-tennis-top-view} for visual illustration
\item \textbf{TCP:} transmission control protocol
\item \textbf{Team}: all team members of the core capstone project, as noted in the list of Authors
\item \textbf{User Side}: the side of the table where the user (player) is standing
\item \textbf{Yaw}: rotation along the z-axis; this rotation angle primarily dictates the panning functionality of the shooting mechanism from the right side to the left side of the table
\end{itemize}

\begin{figure}[H]
   \centering
    %requires the graphicx package
   \caption{Top View of the Tennis Table}
   \label{fig:table-tennis-top-view}
\end{figure}
\subsection{Project Scope}
The system will only attempt to shoot balls from the shooting mechanism straight towards the user side. Notably, the system will not attempt to return any shots from the user. After the user has returned a shot, the Computer Vision (CV) subsystem will be utilized to determine if the user's shot lands on the table or not. Additionally, the characteristics of the shot following any return will be determined by the system's mode and the proficiency of the player if available.
\subsection{Assumptions}
This design assumes the user supplies a functioning webcam, a capable computer to run the software and can connect to the SmartServe system via USB. The computer should have proficient computing power, as the CV subsystem will suffer in proficiency as a result. It is also assumed the use cases described here cover all interactions the user will attempt to have with the system. We assume the user has a ITTF-approved table, an orange table tennis ball and a paddle to use.
\section{System Description}
\subsection{System Architecture}
The system will follow a service-oriented architecture. This means that a central subsystem will interface with several services that serve a single purpose. Some subsystems will be simply told what needs to be done and others will be asked for some return value. This is done to implement separation of concerns where one subsystem doesn't know everything about the system and only what is necessary to satisfy their requirements. It also allows for easy increments of versioning, where one subsystem can be used as long as it is functional and easily swapped out for a newer version with extra features or increased performance. Moreover, this system has heavy timing constraints and an unpredictable environment so some actions must be taken in absence of a service's response. For example, the computer vision may take longer to track a ball depending on its trajectory where the system must shoot another ball in order to keep the user engaged.

\subsection{Subsystems}
The system will be broken down into subsystems with the following purposes: 
\begin{itemize}
\item \textbf{SmartServe}: general management of subsystems
\item \textbf{Computer Vision}:  detection of returns
\item \textbf{Shooting Mechanism}:  shooting the ball toward the user
\item \textbf{Shot Recommendation}: provides best shot
\item \textbf{Data Storage}: storing the data
\item \textbf{Shooting Model}: modelling the shot's trajectory
\item \textbf{User Interface}: taking input from the user and showing output
\end{itemize}
The diagram for this breakdown can be found in Figure \ref{fig:sub}.
\begin{figure}[H]
   \centering
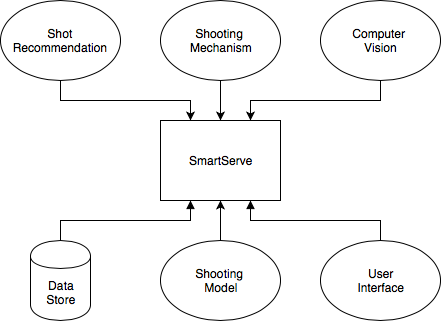
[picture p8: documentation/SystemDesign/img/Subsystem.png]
    % requires the graphicx package
   \caption{Subsystem Breakdown}
   \label{fig:sub}
\end{figure}
\subsection{Use Cases}
The diagram including all use cases can be found in Figure \ref{fig:usecase}. The user-instantiated ones will be described in detail below.
\begin{figure}[H]
   \centering
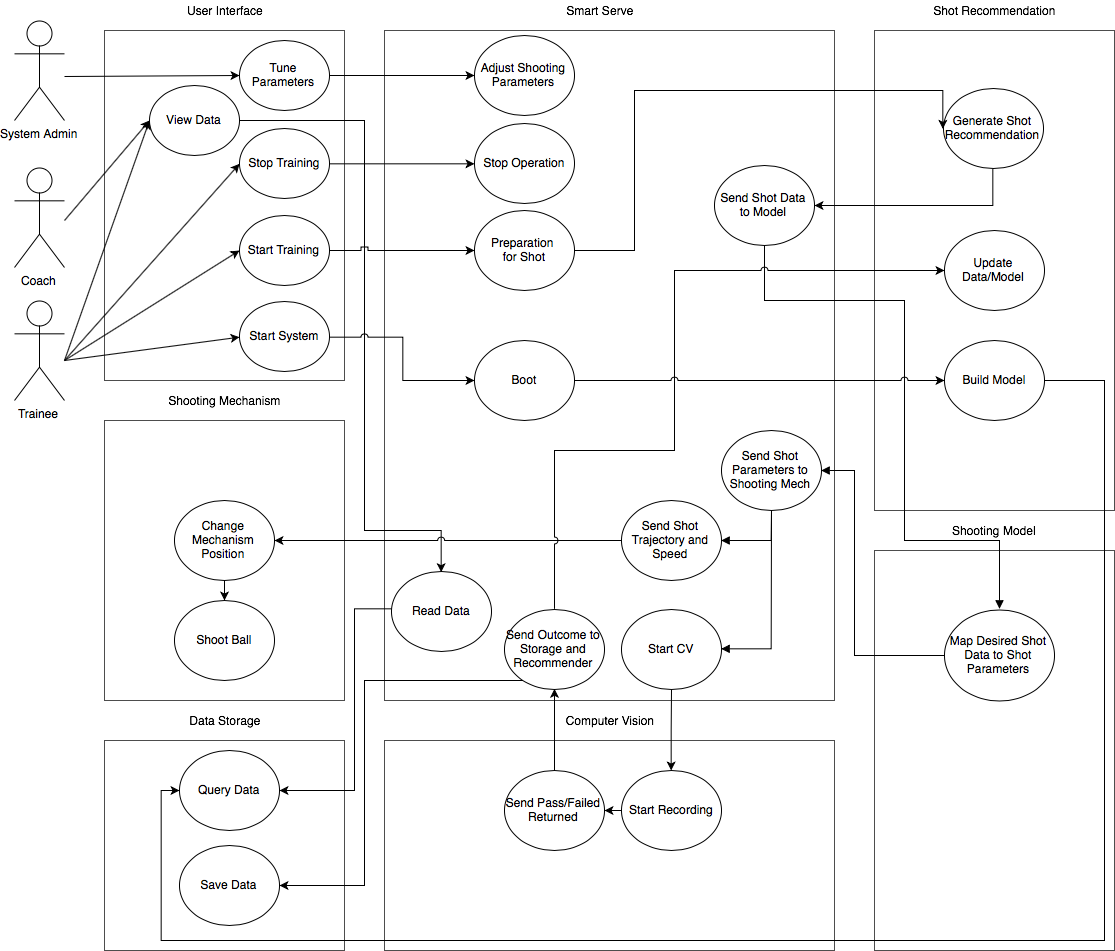
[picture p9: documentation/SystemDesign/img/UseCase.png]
    % requires the graphicx package
   \caption{Use Case Diagram}
   \label{fig:usecase}
\end{figure}
\subsubsection{Start Training}
The user interface will have ways to allow the user to start this action which makes the Smart Serve subsystem prepare for a shot to shoot towards the user. To do this, it needs to request a shot to use from the Shot Recommendation subsystem. The shot includes the following parameters: desired location on the table, the speed of the shot and the angular velocity of the ball. The Smart Serve subsystem can then use the Shooting Model to translate this information into pitch, yaw and angular velocity to shoot the ball so it matches the desired shot. After doing so, it will instruct the shooting mechanism to shoot the ball with the appropriate parameters and start the CV subsystem to begin tracking for a successful return. Only until the CV subsystem returns the pass or failed return data, can it update the Data Storage and Shot Recommendation subsystems with this new information. The former will store the result and the data for the shot together, where the latter will update the model used to generate shot recommendations. Upon completion, it can begin preparing for a new shot.
\begin{figure}[H]
   \centering
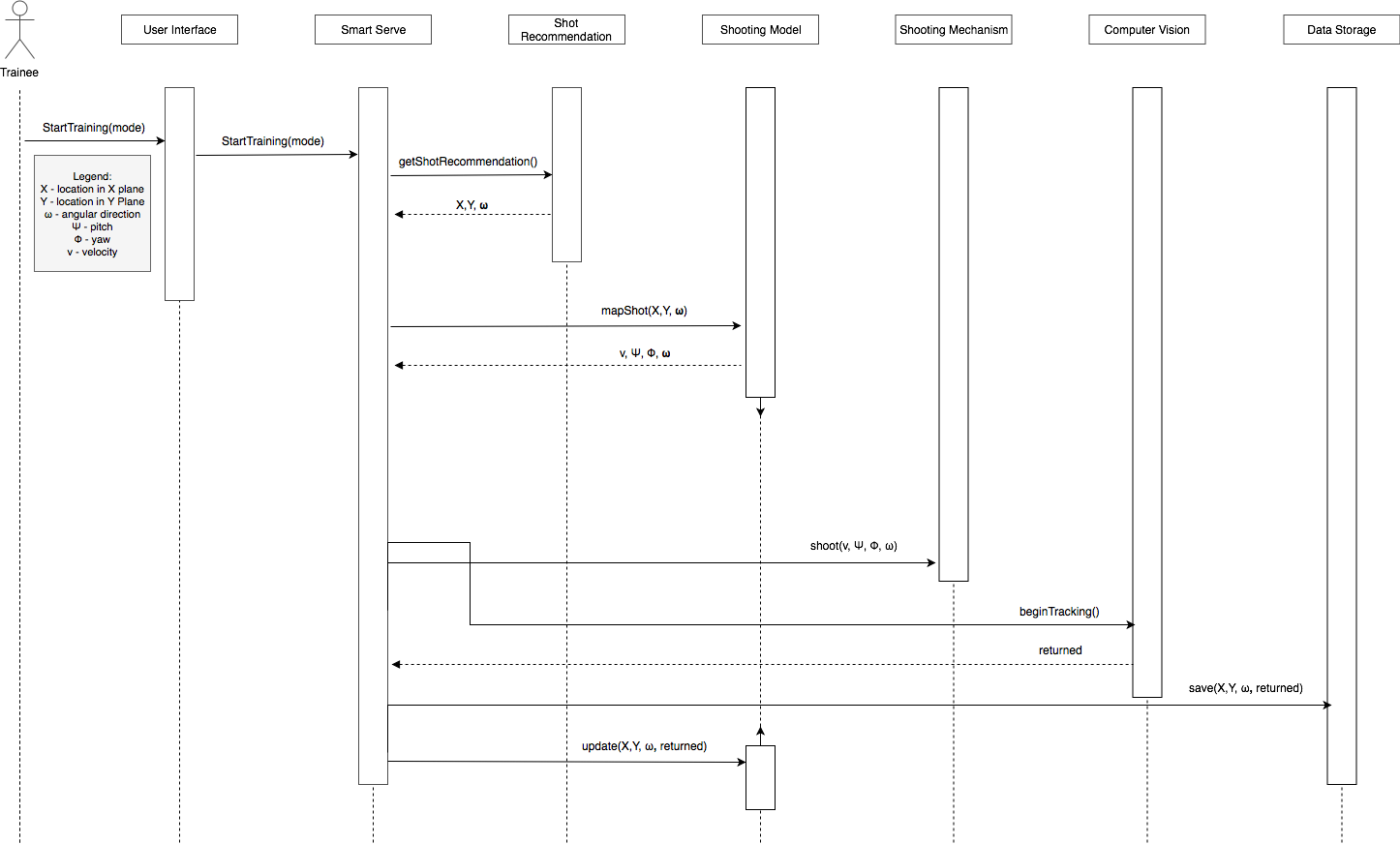
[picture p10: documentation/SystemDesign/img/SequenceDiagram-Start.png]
   
   \caption{Sequence Diagram for Starting Training}
   \label{fig:start}
\end{figure}
\subsubsection{Stop Training}
In the event the user wants to cease training, the user interface will allow this and will halt the system from shooting balls. No data should be written nor shots requested for the shooting mechanism to shoot in order to preserve the integrity of the data being gathered.
\begin{figure}[H]
   \centering
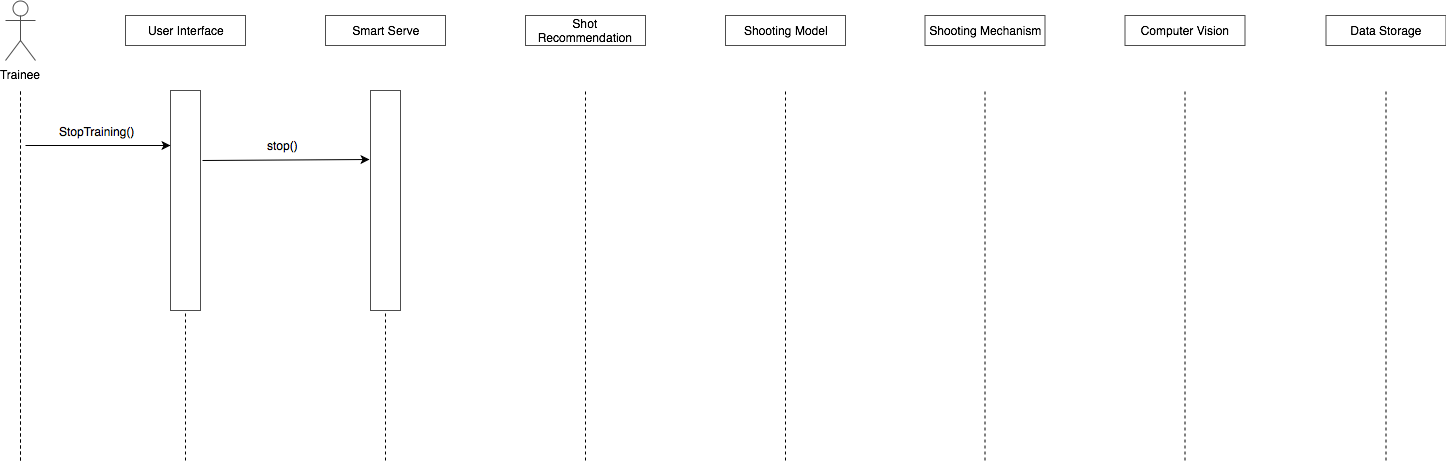
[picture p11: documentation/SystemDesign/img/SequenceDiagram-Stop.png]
   
   \caption{Sequence Diagram for Ceasing Training}
   \label{fig:stop}
\end{figure}
\subsubsection{View Results}
When the user wants to visualize the results of their performance, the user interface should be used. It will use the Smart Serve subsystem to query data from Data Storage and present it in some meaningful way.
\begin{figure}[H]
   \centering
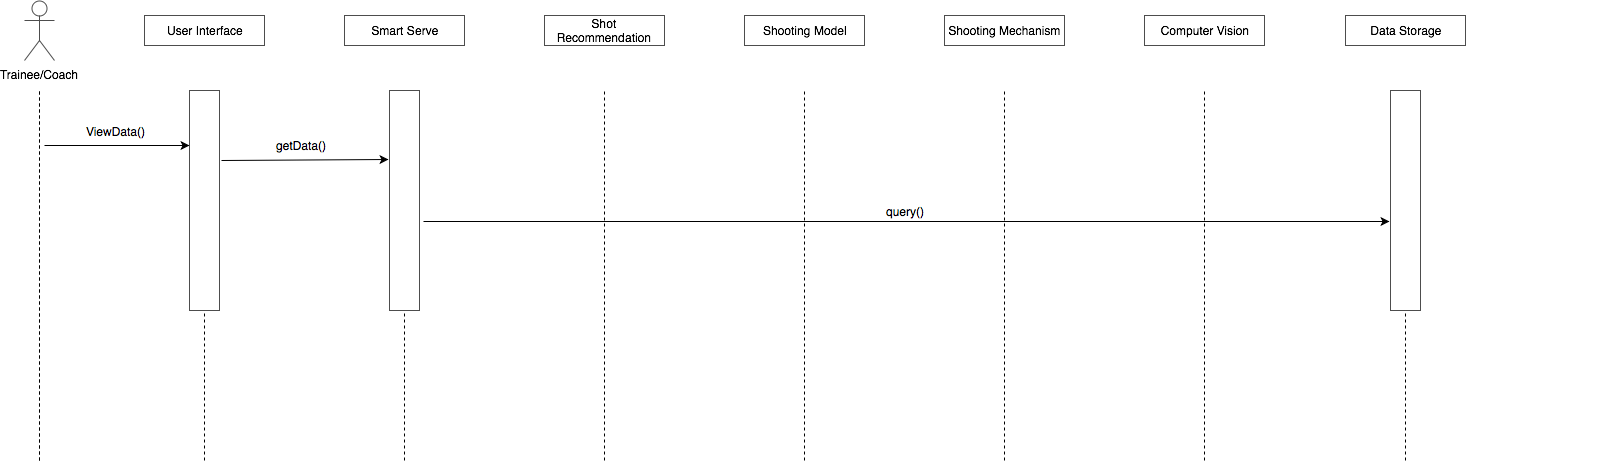
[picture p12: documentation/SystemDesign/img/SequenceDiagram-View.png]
   
   \caption{Sequence Diagram for Viewing Training Results}
   \label{fig:view}
\end{figure}
\subsubsection{Tune Parameters}
The system may need to be adjusted for various lighting, table sizes or environments. The user interface will allow a system administrator to do this in order to directly change values associated for these variables.
\begin{figure}[H]
   \centering
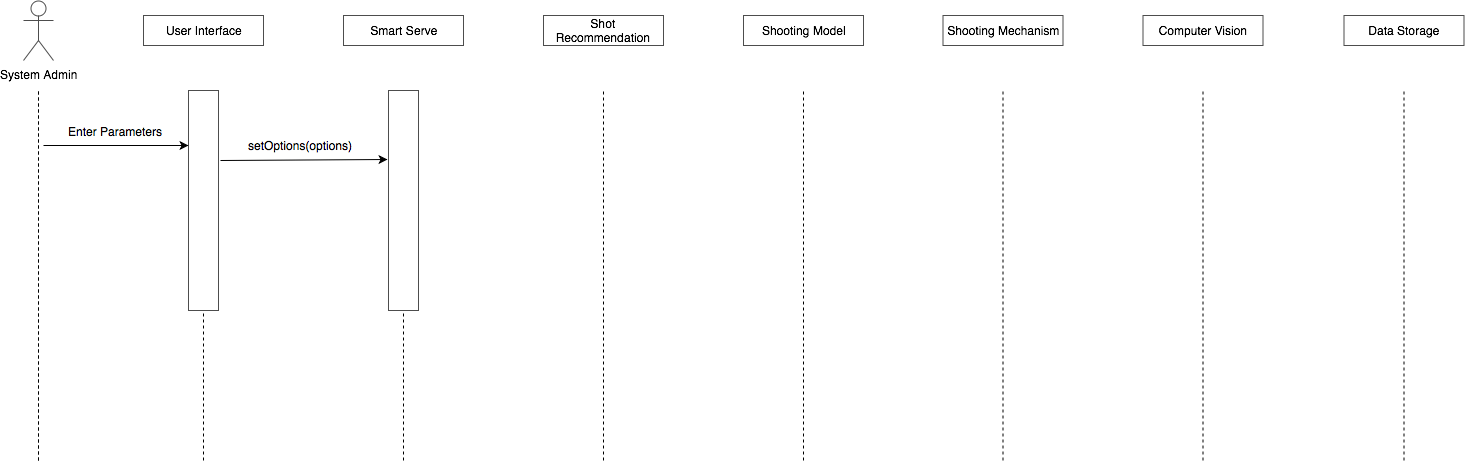
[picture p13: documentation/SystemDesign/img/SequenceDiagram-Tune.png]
   
   \caption{Sequence Diagram for Tuning Parameters}
   \label{fig:tune}
\end{figure}
\subsubsection{Start System}
The user interface will allow the system to be booted which will start the Smart Serve subsystem. This will allow the Shot Recommendation system to build its model based on previous data for the user, if it exists.
\begin{figure}[H]
   \centering
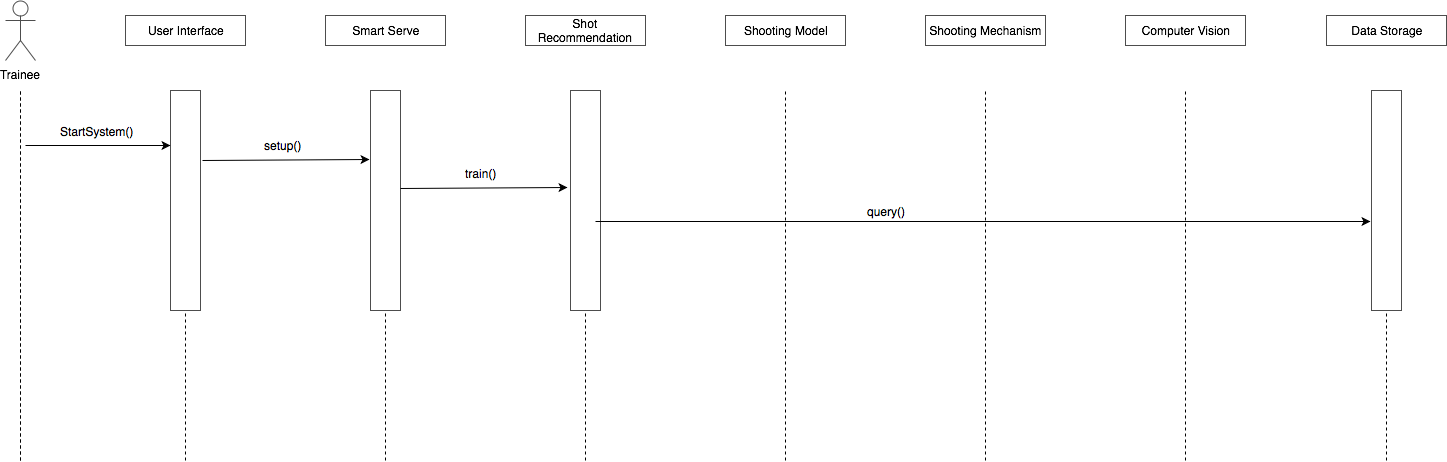
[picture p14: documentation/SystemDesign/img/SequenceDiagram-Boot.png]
   
   \caption{Sequence Diagram for Booting the System}
   \label{fig:boot}
\end{figure}

\subsection{Behaviour Description}
As the behaviour of the system has been discussed previously, this section will describe the expected user behaviour and how they will interact with the system.
\subsubsection{Normal Operation}
The trainee would begin by starting the system from its off state. This will trigger the Start System use case. The user will then trigger the Start Training use case and specify a training mode. This creates the loop of Smart Serve prepping and serving shots for the user. Only until the user triggers the Stop System use case will this loop stop during normal operation. During or after training a user can start the View Data use case to get details on their performance.
\subsubsection{Abnormal Operation}
Although possible, there are some actions a user could take which would be considered abnormal. If a user hits the ball and it immediately leaves the viewable area of the computer vision, whether it never returns or does so after 1.5 seconds, it should be considered a failed return. A user could also replace the table with a different one without calibrating the system to the new table. Furthermore, the user could misplace the system such that it is not centre with the table or at the edge of the table. The proper placement can be found in Figure \ref{fig:table-tennis-top-view}. The system will require the user to load the balls into the shooting mechanism's hopper which will need to be a particular size and colour to work optimally.
\subsubsection{Error Handling}
If the system should encounter an error, it should display the details of it through the User Interface subsystem. In addition to this, it must take measures to ensure the safety of the user and integrity of the system. This includes stopping all training and pending actions for the system to perform. Examples of such errors include a jammed table tennis ball, and an empty mechanism ball hopper.
\subsection{Likely Changes}
Some aspects of the system design will likely change as the project progresses which will be excluded within this document. This is done so the design is considered complete and the next stages of design and implementation can be done. The first likely change would be to the computer vision subsystem, as the introduction of another camera would change the high level design of this subsystem. The additional camera would track a 3rd dimension, which is along the short side of the table. This change would propagate through the system since the Shot Recommendation subsystem would need to consider this new data for recommending new shots. The Data Storage subsystem will also be changed to hold the new data.
\subsection{Unlikely Changes}
The overall architecture of the system will not change, although additional subsystems could be added or existing ones could be changed. The degrees of freedom for a shot will not change. The Smart Serve subsystem will likely not change, although the data being processed between states may change. 
\section{Subsystems Overview}
\subsection{Smart Serve}
The Smart Serve subsystem will provide the means of interfacing with all the subsystems and enforcing timing constraints. For all intents and purposes, it can be considered the main process and hub of the system. In the event a subsystem is taking too long to respond, this subsystem must be able to continue operation to meet timing requirements. The various states and transitions can be found in Figure \ref{fig:fsm}. The FSM (Finite State Machine) diagram shows each state should have an \textit{exit option} if a service takes longer than allowed to preform an action.
\begin{figure}[H]
   \centering
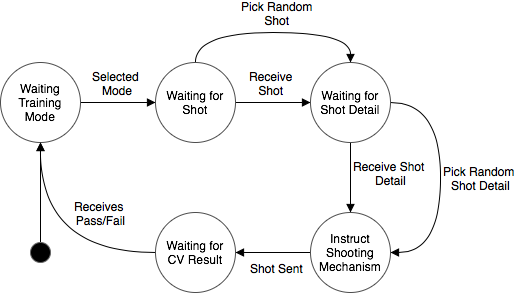
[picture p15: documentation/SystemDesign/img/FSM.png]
   
   \caption{Smart Serve FSM}
   \label{fig:fsm}
\end{figure}

\subsection{Computer Vision}
The Computer Vision subsystem will be a service to the Smart Serve subsystem to determine if a shot is successfully returned. When sent a request to begin tracking the ball, it will do so and return a true when the ball bounces off the table or false when it doesn't. In the event the ball never enters frame, it will assume the return was failed after a fixed amount of time. \\ \\
The FSM will be updated every frame captured within the CV subsystem. Once a frame is captured, the position of the ball will be compared against the previous position and a difference in position can be calculated. Based on how it moved, the state of the FSM will or will not change. Since the ball is being viewed on the System's side, a valid return is when it is moving towards the system, travels downward and then upward while still in frame. The states and transitions of the FSM represent this.
\begin{figure}[H]
   \centering
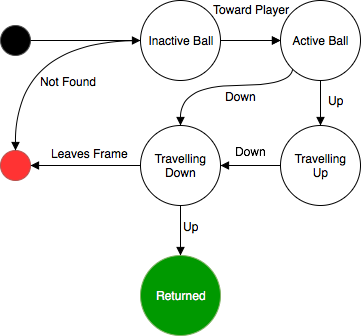
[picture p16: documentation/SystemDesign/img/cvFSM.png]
   
   \caption{CV Finite State Machine}
   \label{fig:cv}
\end{figure}
\subsection{Shot Recommendation}
The Shot Recommendation subsystem will be a service to the Smart Serve subsystem to determine which shot should be taken next. The way the subsystem decides on the shot will be determined by the training mode the user selects. These will include shooting the same shot every time, pseudo-randomly picking a shot or using reinforcement learning algorithms to decide the next shot. The last mode will be based on previous performance by the user. \\ \\
The training mode will utilize a variation of a Upper Confidence Bound (UCB) algorithm. The subsystem will attempt to predict the actual return rate for each type of shot for a particular player by holding a range of values the actual return rate exists within. The initial state is from 0 - 100\% and the range for a individual shot closes when the shot is attempted. The minimum will rise if it is returned successfully and the maximum is lowered if the player misses it. When a shot is needed, the subsystem will select one shot from the shots with the lowest minimum bound since they have the highest chance of being the player's weakest points. This provides the important benefit of exploring different shots at the beginning and exploiting some later in the training phase. 
\subsection{Shooting Model}
The Shooting Model subsystem will be a service to the Smart Serve subsystem which provides the means of mapping a desired shot to the details needed to take the shot. The input and output for the system can be found in Figure \ref{fig:shotmodel}. The output will be an array of many combinations of pitch, yaw, speed and angular velocity that satisfy the input shot details.
\begin{figure}[htbp]
   \centering
    % requires the graphicx package
   \caption{Shooting Model I/O}
   \label{fig:shotmodel}
\end{figure}
\subsection{Data Storage}
The Data Storage subsystem will store all the details for each shot, the user's profile and the return rates for each user. It will need to have interfaces for saving data and querying data out of the system in a variety of formats. Ideally, it will require minimal detail and configuration for the subsystem which uses it due to the variety of implementations of these subsystems.
\subsection{User Interface}
The User Interface subsystem will be the means of translating user requests into actionable requests for the Smart Serve subsystem. The inputs will include a username, password, mode selection and some means of starting and stopping the training. The UI will also need to accept custom parameters for performance data including time ranges and ways to cluster shot types. The output will include custom and useful error messages as well as graphs and tables for performance data.
\subsection{Shooting Mechanism}
The Shooting Mechanism will be the subsystem which fires the ball towards the user. A microcontroller will be used as the point of contact and set any actuators required to fire a specified shot. It must complete this action within 1.5 seconds for the Computer Vision to detect the ball returned by the user. \\\\
The Shooting Mechanism will consist of three main sub parts: Automatic Feeder, Automatic Panning, Ball Shooter. The functionality of the Automatic Feeder part will be to automatically control the feeding rate of the table tennis balls into the shooting barrel and feed the balls into the barrel as initiated by the program. The functionality of the Automatic Panning will be to rotate the entire shooting mechanism or the shooting barrel about the z-axis so the mechanism is able to cover all of the shooting zones as specified in the requirements. Additionally, the functionality of the ball shooter is actually shoot out table tennis balls from the shooting barrel. Please refer to figure \ref{fig:shootingmechanismoutline} for visual representation. \\\\
In terms of electrical components, Arduino UNO microcontroller will be used to control all of the IPO (Input Process Output) processes between the sensors, actuators and Smart Serve. For the ball shooter, a DC Motor will be used as the system will require high speeds and high torques to shoot out table tennis balls. The details on the DC motor can be found below in Table \ref{table:motorspecs} (SAYAL Electronics SKU No. 230437). The DC Motor will be controlled using the PWM method for speed control. Additionally, a Stepper Motor will be utilized for the automatic feeding of the balls into shooting barrel functionality as the Stepper motor would not require any position encoder as well as the stepper motor will have predictable movements. Details on the stepper motor can be found below in Table \ref{table:feedermotorspecs} (Grobotronics SKU No. 19-00012858). For the automatic panning part of the shooting mechanism, a servo or a stepper motor will be utilized however that would be further refined after rigorous prototyping and simulations. Please refer to Figure \ref{fig:electricalwiringdiagrambb}, Figure \ref{fig:electricalwiringdiagramschematic}, and Figure \ref{fig:electricalwiringdiagrampcb} for an overview of Electrical Bread Board, Schematic and PCB layout diagrams of how the Shooting Mechanism system outline.

\begin{table}[H]
\begin{center}
\begin{tabular}{|c|c|}
	\hline 
	Motor Type & DC \\ 
	\hline 
	Operating Voltage & 3V - 6V DC \\ 
	\hline 
	Max. Speed & 17000 rpm \\ 
	\hline 
	Shaft Diameter & 2 mm \\ 
	\hline 
	Torque & 20.72 g-cm \\ 
	\hline 
\end{tabular} 
\caption{Shooting Motor Specifications}
\label{table:motorspecs}
\end{center}

\begin{center}
	\begin{tabular}{|c|c|}
		\hline 
		Motor Type & Uni-polar Gear Stepper with Driver \\ 
		\hline 
		Operating Voltage & 5V DC \\ 
		\hline 
		Max. Speed & 80rpm over-driving with 9V \\ 
		\hline 
		Holding Torque & 350 g-cm \\ 
		\hline 
		Step Angle (output shaft) & 5.625$^{\circ}$/64 \\ 
		\hline 
		Gear Ratio & 1/64 reduction \\ 
		\hline 
		Steps per Rev. & 512 \\ 
		\hline 
		Shaft & Flattened for set-screw attachment \\ 
		\hline 
	\end{tabular} 
	\caption{Feeder Motor Specifications}
	\label{table:feedermotorspecs}
\end{center}
\end{table}

\begin{figure}[H]
   \centering
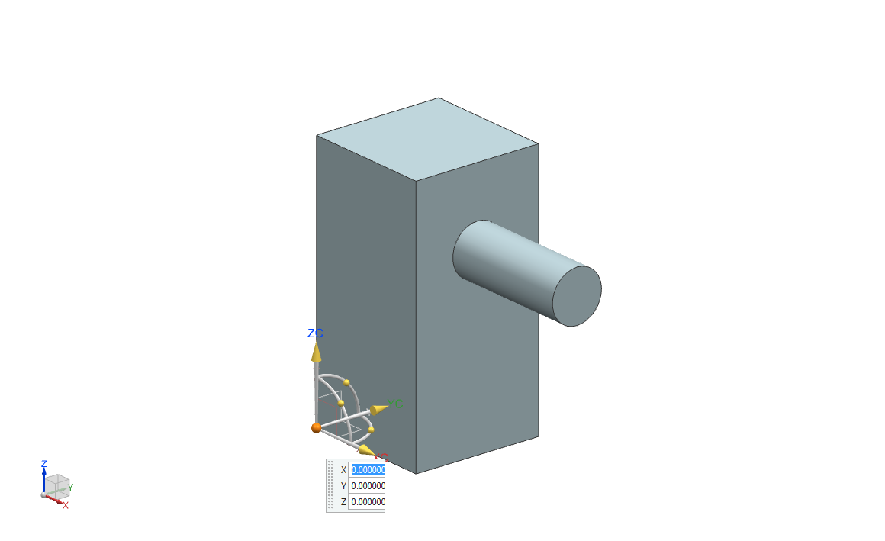
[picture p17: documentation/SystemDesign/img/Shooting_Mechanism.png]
    %requires the graphicx package
   \caption{Shooting Mechanism Rough Outline}
   \label{fig:shootingmechanismoutline}
\end{figure}

\begin{figure}[H]
   \centering
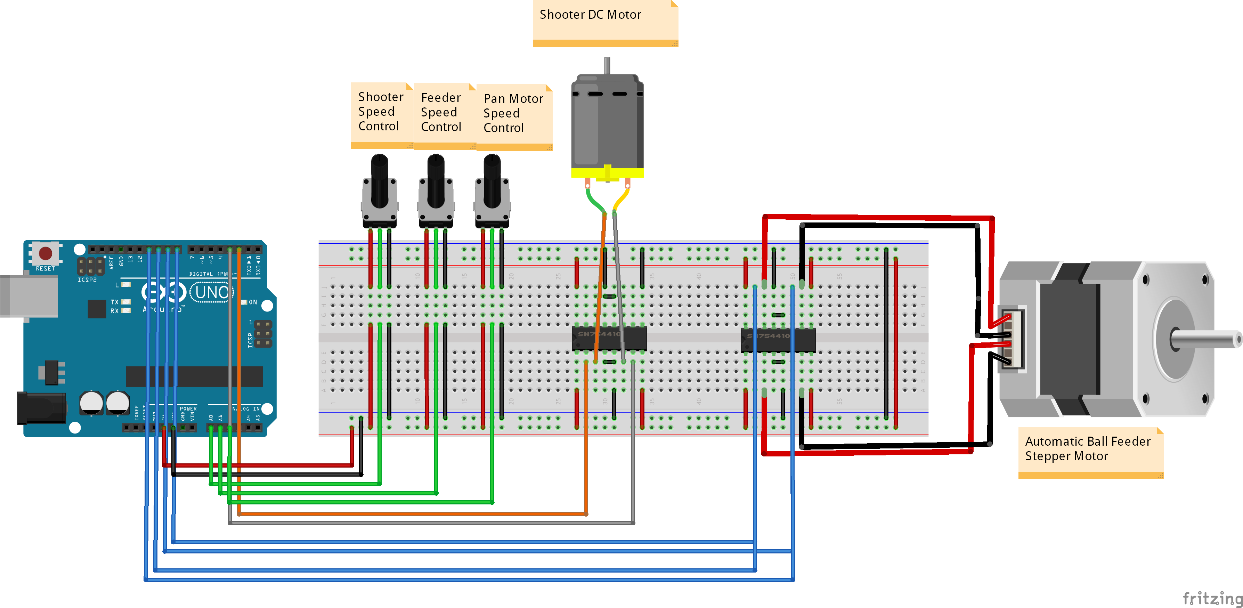
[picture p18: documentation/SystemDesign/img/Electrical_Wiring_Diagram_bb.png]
    %requires the graphicx package
   \caption{Electrical Wiring Diagram - Bread Board}
   \label{fig:electricalwiringdiagrambb}
\end{figure}

\begin{figure}[H]
   \centering
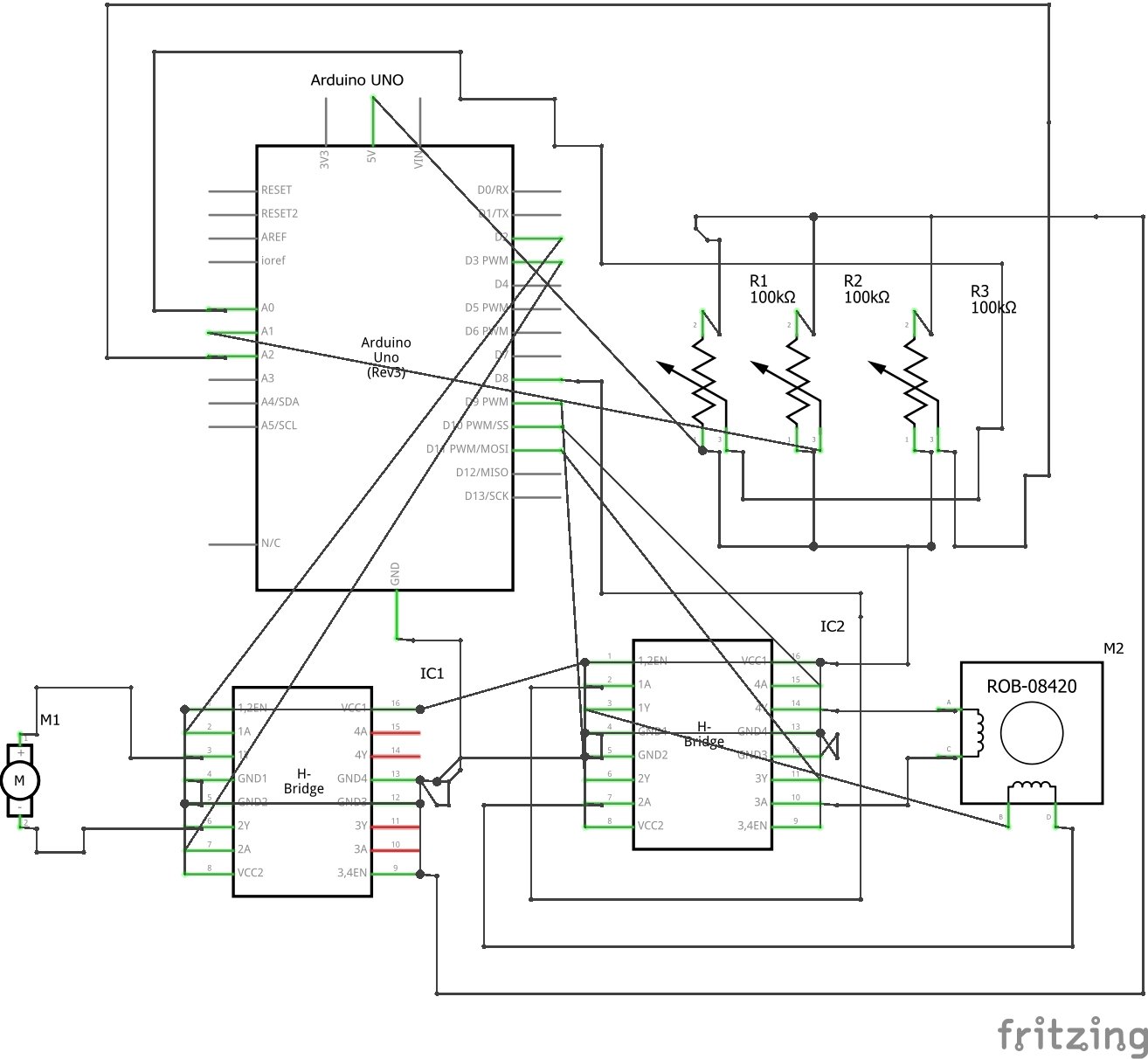
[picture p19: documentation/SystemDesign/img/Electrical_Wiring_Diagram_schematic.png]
    %requires the graphicx package
   \caption{Electrical Wiring Diagram - Schematic}
   \label{fig:electricalwiringdiagramschematic}
\end{figure}

\begin{figure}[H]
   \centering
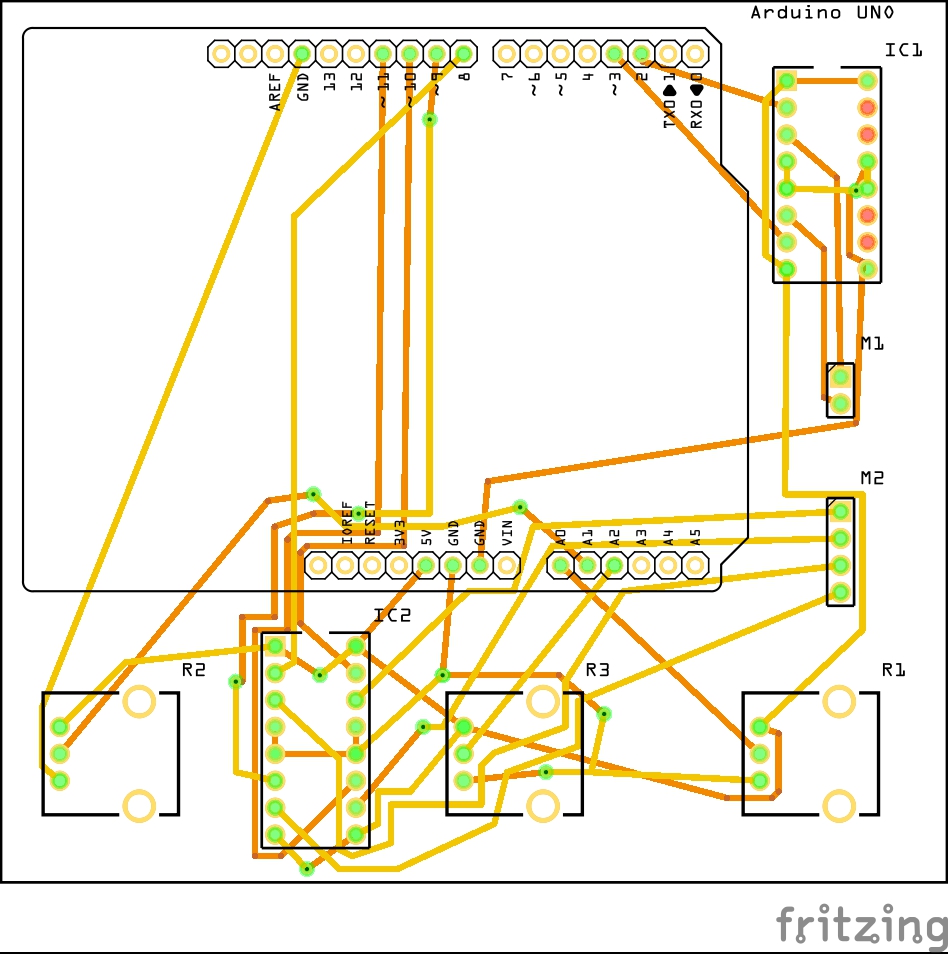
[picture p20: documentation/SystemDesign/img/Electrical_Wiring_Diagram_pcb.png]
    %requires the graphicx package
   \caption{Electrical Wiring Diagram - Printer Circuit Board Trace}
   \label{fig:electricalwiringdiagrampcb}
\end{figure}

\section{Class Responsibility Collaboration (CRC) Cards}
The following sections will include one CRC card for each subsystem. A CRC card contains information pertaining to which requirements a subsystem is responsible for and which subsystems one would collaborate with. This will be used for testing purposes and to track where a given requirement is satisfied. A requirement does not have to be satisfied completely by one subsystem, but a majority of the work must be done by that subsystem.
\subsection{SmartServe}

\begin{table}[H]
\centering
\label{my-label}
\begin{tabular}{ | >{\raggedright\arraybackslash}p{0.4\textwidth} | >{\raggedright\arraybackslash}p{0.4\textwidth} | }
\hline
\multicolumn{2}{|c|}{\textbf{Smart Serve}}             \\ \hline
\textbf{Responsibilities:} & \textbf{Collaborators:} \\ \hline
\begin{itemize}
\item \textbf{F10}: pause the shooting mechanism
\item \textbf{F18}: shoot a ball once the previous has been returned to the system side or 1.5 seconds after the previous shot, whichever is shorter
\item \textbf{P2}:  must include all but previous 3 shots in performance data
\item \textbf{P5}: must support only one user playing at one time
\end{itemize}
&
\begin{itemize}
\item Computer Vision
\item Shot Recommendation
\item Shooting Model
\item Data Storage
\item User Interface
\item Shooting Mechanism
\end{itemize} \\ \hline
\end{tabular}
\caption{Smart Serve CRC Card}
\end{table}

\subsection{Computer Vision}

\begin{table}[H]
\centering
\label{my-label}
\begin{tabular}{ | >{\raggedright\arraybackslash}p{0.4\textwidth} | >{\raggedright\arraybackslash}p{0.4\textwidth} | }
\hline
\multicolumn{2}{|c|}{\textbf{Smart Serve}}             \\ \hline
\textbf{Responsibilities:} & \textbf{Collaborators:} \\ \hline
\begin{itemize}
\item \textbf{F5}: detect a successful return by the user
\item \textbf{OE2}: functional in indoor settings with bright florescent lighting
\end{itemize}
&
\begin{itemize} \item Smart Serve
\end{itemize} \\ \hline
\end{tabular}
\caption{Computer Vision CRC Card}
\end{table}

\subsection{Shot Recommendation}

\begin{table}[H]
\centering
\label{my-label}
\begin{tabular}{ | >{\raggedright\arraybackslash}p{0.4\textwidth} | >{\raggedright\arraybackslash}p{0.4\textwidth} | }
\hline
\multicolumn{2}{|c|}{\textbf{Smart Serve}}             \\ \hline
\textbf{Responsibilities:} & \textbf{Collaborators:} \\ \hline
\begin{itemize}
\item \textbf{F7}: load a previously saved state
\item \textbf{F14}: implements a training mode
\end{itemize}
&
\begin{itemize}
\item Smart Serve
\item Data Storage
\end{itemize} \\ \hline
\end{tabular}
\caption{Shot Recommendation CRC Card}
\end{table}

\subsection{Shooting Model}

\begin{table}[H]
\centering
\label{my-label}
\begin{tabular}{ | >{\raggedright\arraybackslash}p{0.4\textwidth} | >{\raggedright\arraybackslash}p{0.4\textwidth} | }
\hline
\multicolumn{2}{|c|}{\textbf{Smart Serve}}             \\ \hline
\textbf{Responsibilities:} & \textbf{Collaborators:} \\ \hline
\begin{itemize}
\item \textbf{F14}: implements a training mode
\item \textbf{F15}: implements a one-shot mode
\end{itemize}
&
\begin{itemize}
\item Smart Serve
\end{itemize} \\ \hline
\end{tabular}
\caption{Shooting Model CRC Card}
\end{table}

\subsection{Data Storage}

\begin{table}[H]
\centering
\label{my-label}
\begin{tabular}{ | >{\raggedright\arraybackslash}p{0.4\textwidth} | >{\raggedright\arraybackslash}p{0.4\textwidth} | }
\hline
\multicolumn{2}{|c|}{\textbf{Smart Serve}}             \\ \hline
\textbf{Responsibilities:} & \textbf{Collaborators:} \\ \hline
\begin{itemize}
\item \textbf{F6}: saves details for each shot taken by the shooting mechanism
\item \textbf{F8}: allows creation of a new user
\item \textbf{F9}: authenticate users
\item \textbf{P4}: must support 1000 users
\item \textbf{MS2}: able to add new metrics to analyze performance
\item \textbf{S1}: hash all passwords for user profiles
\item \textbf{S2}: encrypt all performance data for each user
\item \textbf{P1}: allow read access for coaches
\end{itemize}
&
\begin{itemize}
\item Shot Recommendation
\item Smart Serve
\end{itemize} \\ \hline
\end{tabular}
\caption{Data Storage CRC Card}
\end{table}

\subsection{User Interface}

\begin{table}[H]
\centering
\label{my-label}
\begin{tabular}{ | >{\raggedright\arraybackslash}p{0.4\textwidth} | >{\raggedright\arraybackslash}p{0.4\textwidth} | }
\hline
\multicolumn{2}{|c|}{\textbf{Smart Serve}}             \\ \hline
\textbf{Responsibilities:} & \textbf{Collaborators:} \\ \hline
\begin{itemize}
\item \textbf{F11}: end the training session
\item \textbf{F12}: resume training session from a paused state
\item \textbf{F13}: display user's performance over a custom time range
\item \textbf{F16}: allows user to adjust training parameters during an active or paused session
\item \textbf{F17}: can be calibrated for a specific table size
\item \textbf{LF1}: have a minimalist design that is easy to navigate through
\item \textbf{UH1}: is intuitive to use
\item \textbf{UH2}: operable using the English language
\item \textbf{P1}: response time for user input must be less than or equal to 100ms
\end{itemize}
&
\begin{itemize}
\item Smart Serve
\end{itemize} \\ \hline
\end{tabular}
\caption{User Interface CRC Card}
\end{table}

\subsection{Shooting Mechanism}

\begin{table}[H]
\centering
\label{my-label}
\begin{tabular}{ | >{\raggedright\arraybackslash}p{0.5\textwidth} | >{\raggedright\arraybackslash}p{0.5\textwidth} | }
\hline
\multicolumn{2}{|c|}{\textbf{Smart Serve}}             \\ \hline
\textbf{Responsibilities:} & \textbf{Collaborators:} \\ \hline
\begin{itemize}
\item \textbf{F1}: shoots the table tennis ball towards the user at various locations
\item \textbf{F2}: shoots the table tennis ball towards the user at various speeds
\item \textbf{F3}: shoots the table tennis ball towards the user at various degrees of Yaw
\item \textbf{F4}: shoots the table tennis ball towards the user with various degrees of roll
\item \textbf{HS1}: always hit the table at least once per shot
\item \textbf{HS2}: not shoot the ball faster than 22 m/s
\item \textbf{HS3}: have no exposed electrical wiring or components
\item \textbf{HS4}: carries warnings around moving parts
\item \textbf{HS5}: has a button to cease all power to system
\end{itemize}
&
\begin{itemize}
\item Smart Serve
\end{itemize} \\ \hline
\end{tabular}
\caption{Shooting Mechanism CRC Card}
\end{table}

\section{Detailed Class Diagram}
The Detailed Class Diagram is shown in Figure \ref{fig:dcd}, found in the Appendix.

\section{Module Guide}
\subsection{SmartServe Modules} % Chris - edited by Sharon
\subsubsection*{Controller}
\textbf{Responsibilities} \\
The controller handles all the timing constraints and sequential events for shooting balls towards the player. It is the interface for the UI to allow the user to preform any and all actions. \\ \\
\textbf{Secrets} \\
The sequence and timing constraints of the shooting procedure. \\ \\
\textbf{MID}
\begin{itemize}
\item \textbf{boot} - none \\ returns: \textit{boolean} \\ description: instantiates all dependancies and ensures services are working as expected
\item \textbf{startTraining} - Mode m \\ returns: \textit{boolean} \\ description: starts the shooting procedure given a certain training Mode
\item \textbf{stopTraining} - none \\ returns: \textit{boolean} \\ description: stops the training procedure
\item \textbf{setShootingParameters} - ShootingParameters sp \\ returns: \textit{boolean} \\ description: sets the shooting parameters for certain table sizes
\end{itemize}

\subsubsection*{ArduinoConnector}
\textbf{Responsibilities} \\
This module is responsible for facilitating the communication with the Arduino which is part of the Shooting Mechanism subsystem (SM). This includes sending and receiving messages as well as ensuring proper testing of the connection is preformed. \\ \\
\textbf{Secrets} \\
The connection to the Arduino. \\ \\
\textbf{MID}
\begin{itemize}
\item \textbf{test} - int port \\ returns: \textit{boolean} \\ description: tests connection to the Arduino
\item \textbf{shoot} - float pitch, float yaw, float angularVelocity \\ returns: \textit{none} \\ description: instructs Arduino to shoot the ball in a certain way
\item \textbf{position} - none \\ returns: \textit{Position} \\ description: returns the position of the mechanism
\end{itemize}

\subsubsection*{ShotRecommendationConnector}
\textbf{Responsibilities} \\
This module is responsible for facilitating the communication with the ShotRecommendation subsystem (SR). This includes sending and receiving messages as well as ensuring proper testing of the connection is preformed. \\ \\
\textbf{Secrets} \\
The connection to the SR. \\ \\
\textbf{MID}
\begin{itemize}
\item \textbf{connect} - int port, [optional] String ip \\ returns: \textit{boolean} \\ description: instantiates all dependancies and ensures services are working as expected
\item \textbf{getRecommendation} - none \\ returns: \textit{Shot} \\ description: returns the shot data to shoot towards the player

\item \textbf{updateModel} - Shot shot, boolean returned \\ returns: \textit{none} \\ description: sends data to SR on whether a R was returned or not
\end{itemize}

\subsubsection*{CVConnector}
\textbf{Responsibilities} \\
This module is responsible for facilitating the communication with the Computer Vision subsystem (CV). This includes sending and receiving messages as well as ensuring proper testing of the connection is preformed. \\ \\
\textbf{Secrets} \\
The connection to the CV system. \\ \\
\textbf{MID}
\begin{itemize}
\item \textbf{connect} - int port \\ returns: \textit{boolean} \\ description: tests connection to CV subsystem
\item \textbf{start} - none \\ returns: \textit{boolean} \\ description: instructs CV to begin tracking and return data for shot

\end{itemize}

\subsubsection*{SQLConnector}
\textbf{Responsibilities} \\
This module is responsible for facilitating the communication with the Data Storage subsystem (DS). This includes sending and receiving messages as well as ensuring proper testing of the connection is preformed. \\ \\
\textbf{Secrets} \\
The connection to the DS. \\ \\
\textbf{MID}
\begin{itemize}
\item \textbf{connect} - int port, [optional] String ip \\ returns: \textit{boolean} \\ description: tests connection to DS on port \textit{port} at the IP Address \textit{ip} or \textit{localhost} if ip is unavailable
\item \textbf{query} - String procedure, Map\textless String, String\textgreater values \\ returns: \textit{ResultSet} \\ description: returns data from database based on procedure ran and values given
\item \textbf{save} - String procedure, Map\textless String, String\textgreater values \\ returns: \textit{boolean} \\ description: returns success information on write to database based on procedure ran and values given
\end{itemize}

\subsubsection*{ShootingParameters}
\textbf{Responsibilities} \\
None. \\ \\
\textbf{Secrets} \\
None. \\ \\
\textbf{MID}
\begin{itemize}
\item \textbf{ShootingParameters} - double tableWidth, double tableLength \\ description: constructs a ShootingParameters object
\end{itemize}

\subsection{Shot Recommendation Modules} % Chris - edited by Sharon
\subsubsection*{Controller}
\textbf{Responsibilities} \\
This module will act as the API interface for the SR. As such, it will accept requests and return the appropriate data. It will also communicate will other modules should a user of this system need to do so. \\ \\
\textbf{Secrets} \\
The process for handling SR requests. \\ \\
\textbf{MID}
\begin{itemize}
\item \textbf{listen} - none \\ returns: \textit{none} \\ description: waits for a request made for a shot
\item \textbf{query} - String procedure, Map\textless String, String\textgreater values, [optional] int port, [optional] String ip \\ returns: \textit{Cursor} \\ description: gets data from a stored procedure using some set of values for a MySQL instance on port \textit{port} at the IP Address \textit{ip}
\end{itemize}

\subsubsection*{Model}
\textbf{Responsibilities} \\
This module will hold the data for each user in such a way information can be extracted. It will contain an internal model which is built from the data and use it to recommend a new shot. \\ \\
\textbf{Secrets} \\
The algorithm to build the model. \\ \\
\textbf{MID}
\begin{itemize}
\item Model \textbf{model} - representation of shot performance data for extracting information
\item \textbf{Model} - none \\ description: constructs a new Model
\item \textbf{train} - Cursor cur \\ returns: \textit{none} \\ description: using some data from Cursor, this will train the model
\item \textbf{next} - none \\ returns: \textit{Shot} \\ description: returns a shot based on the user's past performance
\end{itemize}

\subsection{Shooting Model Modules}
\subsubsection*{Shot}
\textbf{Responsibilities} \\
Specific details (such as yaw and speed) that are required to take the desired shot are stored within this abstract data type module. \\ \\
\textbf{Secrets} \\ 
None \\  \\
\textbf{MID} 
\begin{itemize}
\item \textbf{Shot} - Orientation orientation, double velocity \\ description: constructor to store the shooting model details in an abstract data type.
\item \textbf{toString} - none \\ returns: \textit{String} \\ description: Returns shooting details in a printable string format.
\end{itemize}

\subsubsection*{ShootingModel}
\textbf{Responsibilities} \\
Responsible for mapping a desired shot to the details needed to take the shot. \\ \\
\textbf{Secrets} \\ 
Methods and formulas being used to identify the required details needed to take the desired shot. \\  \\
\textbf{MID} 
\begin{itemize}
\item \textbf{ShootingModel} - double initialHeight, double xInitialHeight, double pitch \\ description: instantiates the ShootingModel subsystem (SModel).
% TODO: Harit change these god awful names
\item \textbf{getShotDetails} - double landingXCoord, double landingYCoord \\ returns: \textit{Shot} \\ description: calculates details to take the desired shot and stores them within the ADT.
\end{itemize}

\subsection{Computer Vision Modules}
\subsubsection*{Detect}
\textbf{Responsibilities} \\
This module detects successful returns from the user, and sends that data to the SmartServe subsystem (SS).\\
\textbf{Secrets} \\ 
Success criteria of returns and how the camera feed is analyzed.\\ 
\textbf{MID} 
\begin{itemize}
\item \textbf{detect} - CameraCapture cap \\ returns: \textit{none} \\ description: Detects if the ball was succesfully returned by the user and calls the Send function
\item \textbf{send} - none \\ returns: \textit{none} \\ description: Sends a signal to SS indicating that a successful return was made
\end{itemize}

\subsubsection*{CameraCapture}
\textbf{Responsibilities} \\
None. \\ \\
\textbf{Secrets} \\
None. \\ \\
\textbf{MID}
\begin{itemize}
\item \textbf{CameraCapture} - none\\ description: constructs a CameraCapture object
\end{itemize}

\subsection{Data Storage Modules}
\subsubsection*{Global}
\textbf{Responsibilities} \\
Communicates with the database to create, delete and update rows in various tables.  \\ \\
\textbf{Secrets} \\
All connection information between the sub-systems, table contents.\\ \\
\textbf{MID} \\
\begin{itemize}
\item User \textbf{user} - String userName, String password, int userId \\ description: representation of a user
\item Shot \textbf{shotType} - int zoneId, int omegaId, int shotId \\ description: representation of a shot type
\item Zone \textbf{zone} -  int zoneId, double xLoc, double yLoc \\ description: representation of a zone on the table, used as a look up table
\item Omega \textbf{omega} - int omegaId, double angle, double velocity \\ description: representation of angular velocity of the ball, used as a look up table
\item ReturnRate \textbf{returnRate} - int userId, int shotId,  Timestamp timeStamp, boolean returned \\ description: return statistics for each user
\item \textbf{signUp} - String userName, String password \\ returns: \textit{none} \\ description: adds a user row to the \textit{User} table
\item \textbf{nextShot} - int zone \\ returns: \textit{Shot} \\ description: determines which shot type to perform
\item \textbf{returned} - Timestamp timeStamp, User user, Shot shot \\ returns: \textit{none} \\ description: updates returnRate table for user for performance statistics
\item \textbf{signIn} - User user \\ returns: \textit{boolean} \\ description: validates and authenticates the user

\end{itemize}

\subsection{Shooting Mechanism Modules}
This module will be specified in the hardware component design of the SM.
\subsection{User Interface Modules}
\subsubsection*{Controller}
\textbf{Responsibilities} \\
Responsible for translating the desired action of the user from the View module to the SS. \\ \\
\textbf{Secrets} \\
Connection between modules and sub-systems. \\ \\
\textbf{MID}
\begin{itemize}
\item \textbf{main} - String[] args \\ returns: \textit{none} \\ description: calls the View module to initialize the UI
\item \textbf{setTrainingMode} - Mode m \\ returns: \textit{none} \\ description: sets mode from View module and sends it to SS
\item \textbf{setShootingParameters} - ShootingParameters \\ returns: \textit{none} \\ description: sets shooting parameters from View module and sends it to SS
\item \textbf{setStatistics} - String statParam \\ returns: \textit{none} \\ description: sets statistics parameters and sends them to View module
\item \textbf{signUp} - User user \\ returns: \textit{none} \\ description: gets user information from view module and sends it to SS
\item \textbf{login} - User user \\ returns: \textit{boolean} \\ description: gets user name and password from the View module and authenticates by calling SS
\end{itemize}
\subsubsection*{View}
\textbf{Responsibilities} \\
The view module will contain all the actual visual aspects of the system that the user will interact with. This includes text, pictures, buttons, etc. \\ \\
\textbf{Secrets} \\
The structure and implementation of the view. \\ \\
\textbf{MID}
\begin{itemize}
\item \textbf{start} - none \\ returns: \textit{none} \\ description: general user interface code, called to initiate UI
\item \textbf{selectMode} - MouseEvent me\\ returns: \textit{Mode} \\ description: listens for a mouse click on mode types, and returns that mode
\item \textbf{calibrate} - none \\ returns: \textit{ShootingParameters} \\ description: collects user input for table size in order to calibrate the system
\item \textbf{startTrainingBtn} - MouseEvent me \\ returns: \textit{boolean} \\ description: listens for mouse click on start training button
\item \textbf{stopTrainingBtn} - MouseEvent me \\ returns: \textit{boolean} \\ description: listens for mouse click on stop training button
\item \textbf{viewStatsBtn} - MouseEvent me \\ returns: \textit{none} \\ description: listens for mouse click on statistics button and displays statistics to the user
\item \textbf{signUpBtn} - MouseEvent me \\ returns: \textit{User} \\ description: listens for mouse click on sign up button and collects user information
\item \textbf{loginBtn} - MouseEvent me \\ returns: \textit{User} \\ description: listens for mouse click on sign in button and displays profile if authenticated properly
\item \textbf{displayError} - Exception exceptionLog \\ returns: \textit{none} \\ description: allows user to read an error or download a log file to send to development team
\end{itemize}

\section{Communication Protocols} % Chris
\subsection{SmartServe to Shot Recommendation}
The SR will use Python to leverage machine learning libraries like SciKit Learn and the SS will be implemented in Java. In order for the SS to communicate to the SR, it will make an HTTP request with some data and receive an HTTP response encoded using JSON. This allows the use of a reliable means of communication and flexibility to host the SR remotely if need be. \\ \\
The SS will make a GET request to the SR for requesting a shot to use and can make POST request to give data regarding whether a shot was returned or not. In the event the HTTP request takes too long, the SS should handle it accordingly by timing out and using random shots or continuing the program. \\ \\
HTTP libraries are standard in Java and a microframework for handling HTTP requests can be used for Python like \href{http://flask.pocoo.org}{flask}.
\subsection{SmartServe to Shooting Mechanism}
The SM will implement an interface using an Arduino. The SS will use libraries for communicating to the Arduino to communicate to the SM which can be found \href{http://fizzed.com/oss/rxtx-for-java}{here} for 64-bit Windows and Linux installations and \href{http://blog.iharder.net/2009/08/18/rxtx-java-6-and-librxtxserial-jnilib-on-intel-mac-os-x/}{here} for 64-bit macOS installations. The SS does not need a response from the system, as it will tell the SM where to shoot and how to do so but does not need a response.
\subsection{SmartServe to Computer Vision}
The SS will communicate to the CV via sockets over the TCP protocol using the Java Networking libraries and the Python socket libraries. The SS will initiate the communication to start tracking and expect a return value based on whether it was returned or not. The SS will timeout in the event the CV does not return a value after 1.5 seconds.
\subsection{SmartServe to User Interface}
The SS and the User Interface subsystem (UI) will both be programmed using Java. The UI system can interface with the SS by calling exposed public methods based on user input.
\subsection{SmartServe to ShootingModel}
The SS and the SModel will both be programmed using Java. The SS system can interface with the SModel by calling exposed public methods based on user input.
\subsection{SmartServe to Data Storage}
The SS is programmed in Java and the DS will be implemented using Stored Procedures held in a MySQL database instance. In order for the SS to use the DS, a \href{https://dev.mysql.com/downloads/connector/j/5.1.html}{SQLConnector} can be used to do so.
\subsection{Shot Recommendation to Data Storage}
The SR is programmed in Python and the DS will be implemented using Stored Procedures held in a MySQL database instance. In order for the SR to use the DS, a \href{https://dev.mysql.com/doc/connector-python/en/}{SQLConnector} can be used to do so.

\section{Hardware Design}
\subsection{Mechanical Components}
\subsubsection*{Shift Adapter}
The shaft adapter is designed to fit snugly on the stepper motor shaft and provides a more robust connection with the \textit{spinning feeder cutout}. The shaft adapter is designed to allow the feeder cutout to sit at a precise height where it could rotate without any obstructions and push the table tennis balls into the \textit{Inner Tube}. The shaft adapter will bring the spinning feeder cutout to a height such that the contant point of the ball is in the middle (biggest diameter of the ball).

\begin{center}
\begin{minipage}[b]{0.6\textwidth}
\begin{figure}[H]
  \centering
  \begin{minipage}[b]{0.4\textwidth}
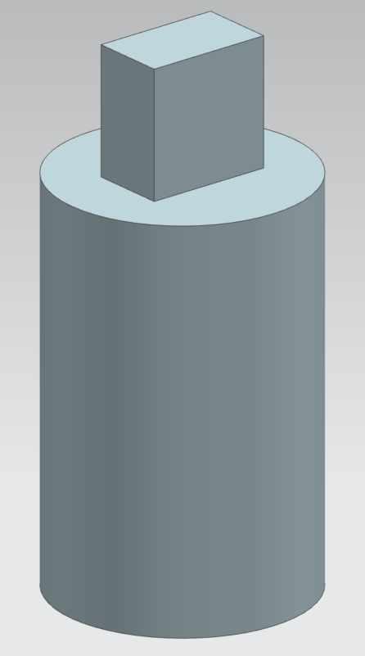
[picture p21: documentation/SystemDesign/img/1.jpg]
    
    \caption{Shaft Adapter 3D}
  \end{minipage}
  \hfill
  \begin{minipage}[b]{0.4\textwidth}
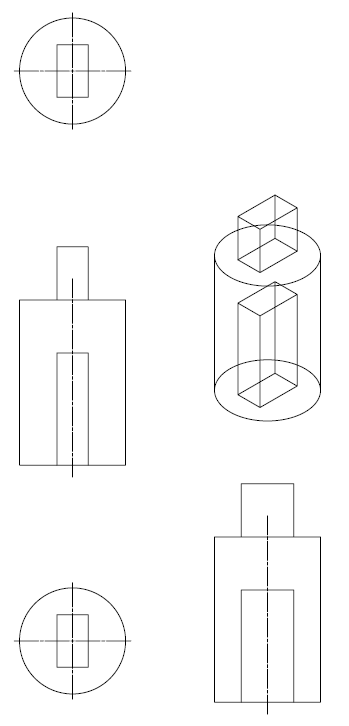
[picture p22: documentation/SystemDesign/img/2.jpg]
    
    \caption{2D Engineering Drawing of Shaft Adapter}
  \end{minipage}
\end{figure}
\end{minipage}
\end{center}

\subsubsection*{Panning Control}
The functionality of the Automatic Panning will be to rotate the entire shooting mechanism or the shooting barrel about the z-axis so the mechanism is able to cover all of the shooting zones as specified in the requirements. \\ \\
The components designed for the panning stage include an acrylic base plate, a rapid prototyped worm wheel gear ring, the worm, and a motor bracket. The base plate clearance mounting holes were made using a workshop drill press / milling machine. The rapid prototyped stepper motor bracket is mounted to the base plate and adjusted so that correct gear engagement is achieved. The Lazy Susan bearing is positioned 10 mm above the plate using spacers and longer \#6?32 screws, washers, and nuts. The worm gear is designed as a ring shape to reduce rapid prototyping material consumption. A corresponding hole pattern mates to the top plate of the Lazy Susan bearing. The optical switch is used to home the system at power up and align the system in the direction required with a reference and from there on the system will always be aware of its position. Optical switches allow for high repeatability making it a very applicable sensor to use in the prototype. 

\begin{center}
\begin{minipage}[b]{0.8\textwidth}
\begin{figure}[H]
  \centering
  \begin{minipage}[b]{0.4\textwidth}
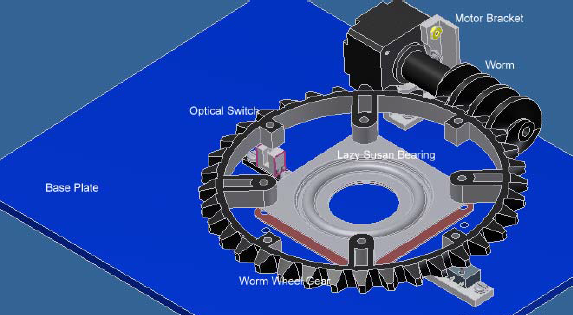
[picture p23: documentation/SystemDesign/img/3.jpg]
    
    \caption{Base Design and Assembly}
  \end{minipage}
  \hfill
  \begin{minipage}[b]{0.4\textwidth}
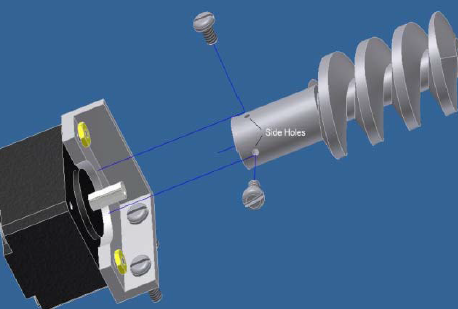
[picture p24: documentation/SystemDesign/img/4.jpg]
    
    \caption{Worm Gear Coupler}
  \end{minipage}
\end{figure}
\end{minipage}
\end{center}

\begin{figure}[H]
   \centering
    % requires the graphicx package
   \caption{Azimuth Stage Autodesk Inventor Design Accelerator Worm Gear Parameters}
   \label{fig:hw5}
\end{figure}

\subsubsection*{Spinning Feeder Cutout}
The spinning feeder cutout is fixed to the shaft of the stepper motor inside the bucket to guide the table tennis balls into the \textit{Inner Tube}. The cutout is laser cut from a thin and sturdy sheet of wood so it has enough thickness (contact surface area) to easily push the table tennis balls around. There will be a lot of balls going in and out of the feeder cutout continuously so it has the sharp edges to hold the ball in once its captured and 45mm diameter semi circles to easily allow the 40mm table tennis balls to slide into the pockets.  

\begin{figure}[H]
   \centering
    % requires the graphicx package
   \caption{Feeder Cutout from topview for laser cutting  }
   \label{fig:hw6}
\end{figure}

\subsubsection*{Inner Tube}
The inner tube is designed to hold table tennis balls to be shot out by the shooting mechanism, as well as have solid support hold the shooting mechanism pipe structure. The diameter of the inner tube is 45mm to allow the ball to be easily fed into the tube but restrict jittering when traveling through the pipe.

\begin{figure}[H]
   \centering
    % requires the graphicx package
   \caption{CAD design of a Inner Tube }
   \label{fig:hw7}
\end{figure}

\subsubsection*{Motor Bracket and Outer Tube}
A custom designed motor bracket is used to mount the DC motor onto the outer PVC tube to create our preliminary shooting mechanism. The motor has a cylindrical housing thus making it difficult to fix onto anything especially onto another cylindrical object, the Outer Tube. The motor has to be mounted securely and tightly to minimize the vibrations into the shooting mechanism which could translate onto the entire system.  

\begin{center}
\begin{minipage}[b]{1.0\textwidth}
\begin{figure}[H]
  \centering
  \begin{minipage}[b]{0.2\textwidth}
    
    \caption{Motor Bracket}
  \end{minipage}
  \hfill
  \begin{minipage}[b]{0.2\textwidth}
    
    \caption{Outer Tube }
  \end{minipage}
  \hfill
  \begin{minipage}[b]{0.2\textwidth}
    
    \caption{Motor with Motor Bracket attached to the Outer Tube }
  \end{minipage}
\end{figure}
\end{minipage}
\end{center}

\subsubsection*{Roll Control}
The roll control part will act as a manual control for the user to decide the type of spin to give the table tennis ball for the current session. The roll control part acts as the male end of a locking mechanism, which will fix the shooter in either a 0, 90, 180, or 270 degree angle. With the roll control settings, the user will be able to manually change the roll setting to experience a topspin, backspin, and left or right spin.The roll control part will be fixed on the base end of the inner shaft of the shooter. The outer shaft of the shooter will then be able to lock into the desired position.

\begin{center}
\begin{minipage}[b]{0.8\textwidth}
\begin{figure}[H]
  \centering
  \begin{minipage}[b]{0.4\textwidth}
    
    \caption{CAD design for Roll Control component }
  \end{minipage}
  \hfill
  \begin{minipage}[b]{0.4\textwidth}
    
    \caption{2D Engineering Drawing of Roll Control Component}
  \end{minipage}
\end{figure}
\end{minipage}
\end{center}

\subsubsection*{Base, Support Brackets and Bucket}
The base is made out of a hardwood and laser cut to an appropriate size. The base acts as a fixture to attach the bucket supports to the azimuth stage. There are two metal support brackets which are made out of stainless steel, and lift the bucket to an appropriate height above the base. The bottom of the supports are screwed into the hardwood base, and the top of the supports are bolted to the bucket. The bucket is 8in x 7in and is large enough to hold at least 20 balls without overfilling.

\begin{center}
\begin{minipage}[b]{0.8\textwidth}
\begin{figure}[H]
  \centering
  \begin{minipage}[b]{0.4\textwidth}
    
    \caption{Base with Support Brackets attached }
  \end{minipage}
  \hfill
  \begin{minipage}[b]{0.4\textwidth}
    
    \caption{Bucket with Inner Tune and Roll Control attached }
  \end{minipage}
\end{figure}
\end{minipage}
\end{center}

\subsubsection*{Pitch Control}
The pitch control consists of a screw that pierces through the support beam and bucket, to hold the shooter at a certain angle. The range of angles are as followed: -15°,0°,15°,30°,45°, and are set by pre drilled holes in the bucket. This design needs to be optimized with a bolt in order to further secure the pitch and eliminate error.

\begin{center}
\begin{minipage}[b]{0.6\textwidth}
\begin{figure}[H]
  \centering
  \begin{minipage}[b]{0.4\textwidth}
    
    \caption{Pitch Control slots }
  \end{minipage}
  \hfill
  \begin{minipage}[b]{0.4\textwidth}
    
    \caption{Pitch Control Holding Pin from Inside }
  \end{minipage}
\end{figure}
\end{minipage}
\end{center}
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

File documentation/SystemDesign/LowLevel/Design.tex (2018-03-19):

\documentclass[11pt]{article}
\usepackage{geometry}
\geometry{letterpaper}

\usepackage{graphicx}
\usepackage{amssymb}
\usepackage{float}
\usepackage{tabularx}
\usepackage{multicol}
\usepackage{rotating}
\usepackage{hyperref}
\hypersetup{
    colorlinks,
    citecolor=black,
    filecolor=blue,
    linkcolor=black,
    urlcolor=black
}

\begin{document}

\begin{titlepage}
	\newcommand{\HRule}{\rule{\linewidth}{0.2mm}}
	\begin{center}
	\textsc{\LARGE McMaster University}\\[1.5cm]

	\textsc{\Large SmartServe}\\[0.5cm]
	\textsc{\large Software \& Mechatronics Capstone}\\[0.5cm]

	\HRule\\[0.4cm]
		{\huge\bfseries Component Design}\\[0.4cm]
	\HRule\\[0.4cm]

	\begin{minipage}[t][][t]{0.5\textwidth}
		\begin{flushleft} \large
			\emph{Authors:}\\
			Christopher McDonald - \textit{001312456} \\
			Harit Patel - \textit{001317372}\\
			Janak Patel - \textit{001307060} \\
			Jared Rayner - \textit{001311702}\\
			Nisarg Patel - \textit{001322805} \\
			Sam Hamel - \textit{001321692} \\
			Sharon Platkin - \textit{001316625} \\
		\end{flushleft}
	\end{minipage}
	~
	\begin{minipage}[t][][t]{0.4\textwidth}
		\begin{flushright} \large
			\emph{Professor:} \\
			Dr. Alan Wassyng \\[0.4cm]
			\emph{Teaching Assistants:} \\
			Bennett Mackenzie \\
			Nicholas Annable \\
			Stephen Wynn-Williams \\
			Viktor Smirnov
		\end{flushright}
	\end{minipage}\\[2cm]

	 \\
	{\large Last compiled on \today}
	\end{center}

\end{titlepage}

\tableofcontents
\listoffigures
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

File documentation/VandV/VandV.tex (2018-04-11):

\documentclass[11pt]{article}
\usepackage{geometry}
\geometry{letterpaper}

\usepackage{graphicx}
\usepackage{amssymb}
\usepackage{float}
\usepackage{tabularx}
\usepackage{multicol}
\usepackage{hyperref}
\hypersetup{
    colorlinks,
    citecolor=black,
    filecolor=blue,
    linkcolor=black,
    urlcolor=blue
}

\begin{document}

\begin{titlepage}
	\newcommand{\HRule}{\rule{\linewidth}{0.2mm}}
	\begin{center}
	\textsc{\LARGE McMaster University}\\[1.5cm]

	\textsc{\Large SmartServe}\\[0.5cm]
	\textsc{\large Software \& Mechatronics Capstone}\\[0.5cm]

	\HRule\\[0.4cm]
		{\huge\bfseries Verification and Validation}\\[0.4cm]
	\HRule\\[0.4cm]

	\begin{minipage}[t][][t]{0.5\textwidth}
		\begin{flushleft} \large
			\emph{Authors:}\\
			Christopher McDonald - \textit{001312456} \\
			Harit Patel - \textit{001317372}\\
			Janak Patel - \textit{001307060} \\
			Jared Rayner - \textit{001311702}\\
			Nisarg Patel - \textit{001322805} \\
			Sam Hamel - \textit{001321692} \\
			Sharon Platkin - \textit{001316625} \\
		\end{flushleft}
	\end{minipage}
	~
	\begin{minipage}[t][][t]{0.4\textwidth}
		\begin{flushright} \large
			\emph{Professor:} \\
			Dr. Alan Wassyng \\[0.4cm]
			\emph{Teaching Assistants:} \\
			Bennett Mackenzie \\
			Nicholas Annable \\
			Stephen Wynn-Williams \\
			Viktor Smirnov
		\end{flushright}
	\end{minipage}\\[2cm]

	 \\
	{\large Last compiled on \today}
	\end{center}

\end{titlepage}

\tableofcontents
\listoffigures
\listoftables
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

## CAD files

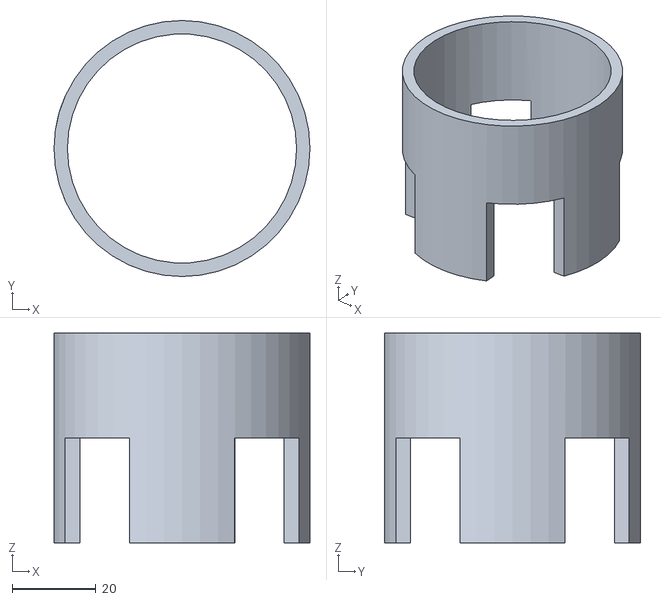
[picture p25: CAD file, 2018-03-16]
hw/3D Print Files/MaleRollControl.stl
61.0 x 61.0 x 50.0

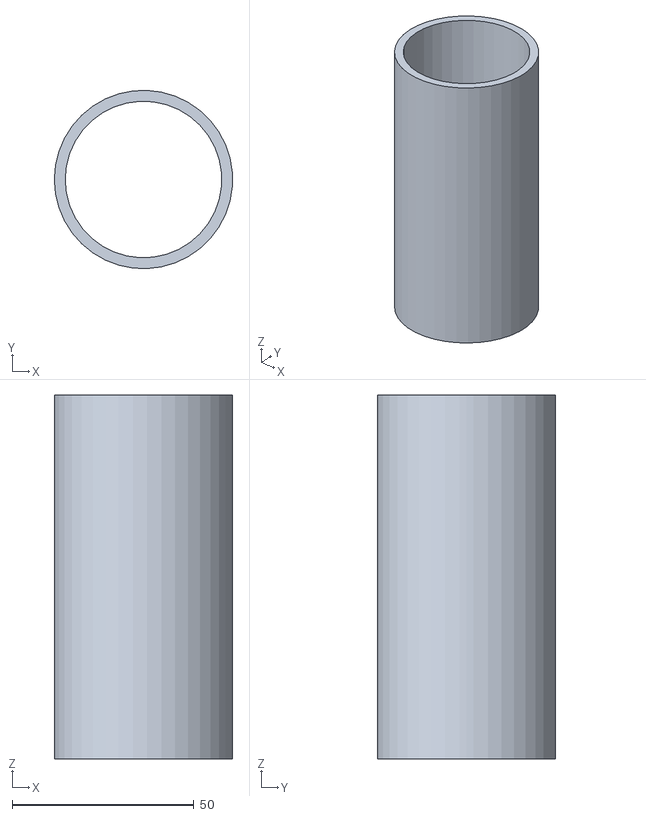
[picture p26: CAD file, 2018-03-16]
hw/3D Print Files/Inner_PVC_Tube_Prototype.stl
49.0 x 49.0 x 100.0

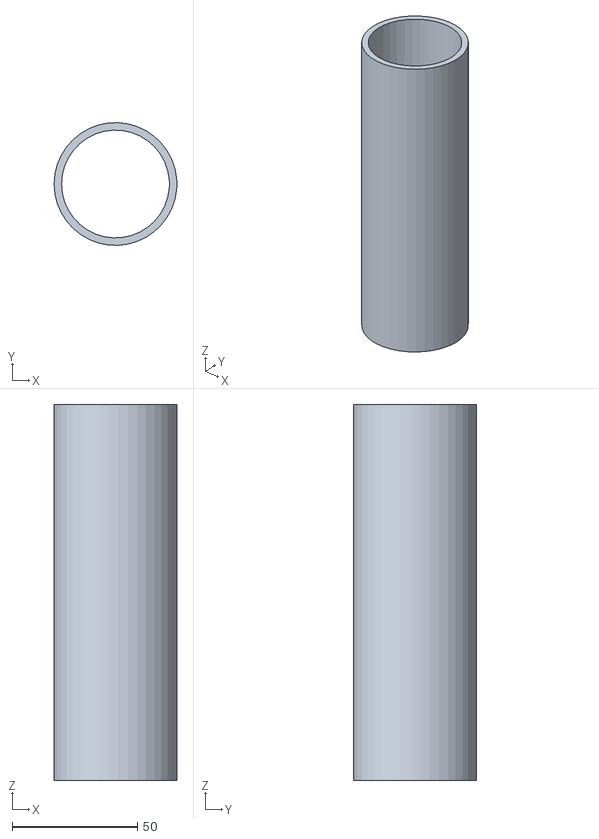
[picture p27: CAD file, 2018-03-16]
hw/3D Print Files/Inner_PVC_Tube_Prototype_15cm.stl
49.0 x 49.0 x 150.0

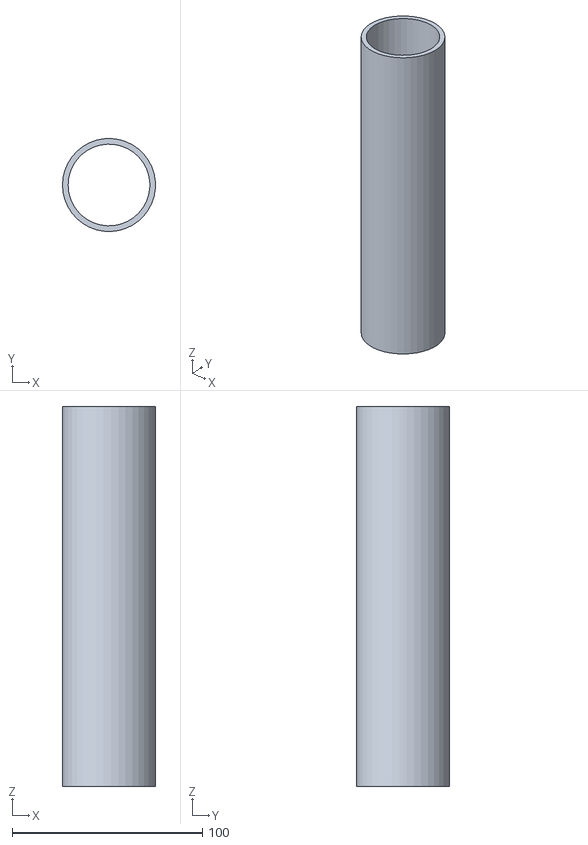
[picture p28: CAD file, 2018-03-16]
hw/3D Print Files/Inner_PVC_Tube_Prototype_20cm.stl
49.0 x 49.0 x 200.0

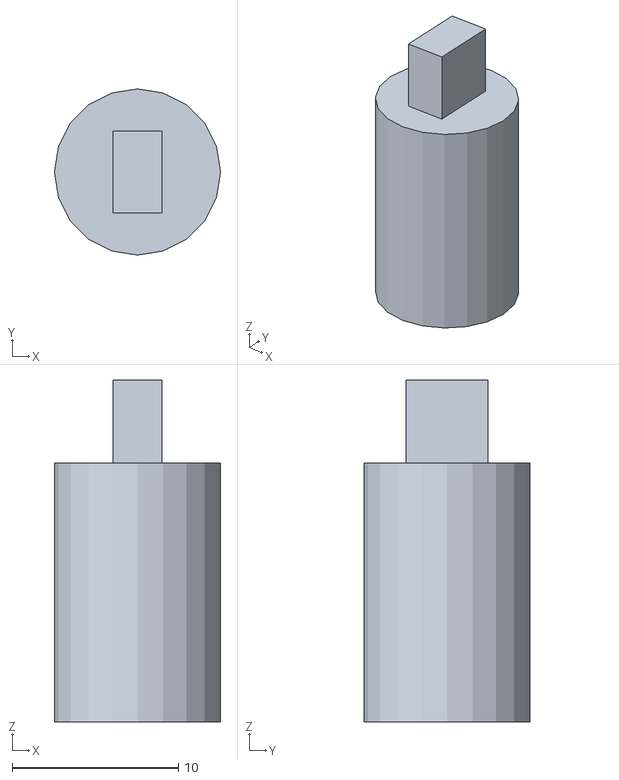
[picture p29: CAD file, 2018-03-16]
hw/3D Print Files/Shaft Adapter for Automatic Feeder.stl
10.0 x 10.0 x 20.6

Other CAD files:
hw/Design/Feeder Cutout.prt
hw/Design/MaleRollControl.prt
hw/design/Inner_PVC_Tube_Prototype.prt
hw/design/Shaft Adapter for Automatic Feeder.prt
hw/design/Table Tennis Table.prt

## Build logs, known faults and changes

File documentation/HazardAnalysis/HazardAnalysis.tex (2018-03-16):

\documentclass[11pt]{article}
\usepackage{geometry}
\geometry{letterpaper}

% TODO: roadmap

\usepackage{graphicx}
\usepackage{amssymb}
\usepackage{float}
\usepackage{tabularx}
\usepackage{multicol}
\usepackage{hyperref}
\hypersetup{
    colorlinks,
    citecolor=black,
    filecolor=blue,
    linkcolor=black,
    urlcolor=blue
}

\begin{document}

\begin{titlepage}
	\newcommand{\HRule}{\rule{\linewidth}{0.2mm}}
	\begin{center}
	\textsc{\LARGE McMaster University}\\[1.5cm]

	\textsc{\Large SmartServe}\\[0.5cm]
	\textsc{\large Software \& Mechatronics Capstone}\\[0.5cm]

	\HRule\\[0.4cm]
		{\huge\bfseries Hazard Analysis}\\[0.4cm]
	\HRule\\[0.4cm]

	\begin{minipage}[t][][t]{0.5\textwidth}
		\begin{flushleft} \large
			\emph{Authors:}\\
			Christopher McDonald - \textit{001312456} \\
			Harit Patel - \textit{001317372}\\
			Janak Patel - \textit{001307060} \\
			Jared Rayner - \textit{001311702}\\
			Nisarg Patel - \textit{001322805} \\
			Sam Hamel - \textit{001321692} \\
			Sharon Platkin - \textit{001316625} \\
		\end{flushleft}
	\end{minipage}
	~
	\begin{minipage}[t][][t]{0.4\textwidth}
		\begin{flushright} \large
			\emph{Professor:} \\
			Dr. Alan Wassyng \\[0.4cm]
			\emph{Teaching Assistants:} \\
			Bennett Mackenzie \\
			Nicholas Annable \\
			Stephen Wynn-Williams \\
			Viktor Smirnov
		\end{flushright}
	\end{minipage}\\[2cm]

	 \\
	{\large Last compiled on \today}
	\end{center}

\end{titlepage}

\tableofcontents
\listoffigures

\vfill
\begin{figure}[H]
   \centering
   \noindent\begin{tabularx}{\textwidth}{| >{\centering\arraybackslash}m{0.2\textwidth} | >{\centering\arraybackslash}m{0.2\textwidth} | >{\centering\arraybackslash}m{0.2\textwidth} | >{\centering\arraybackslash}m{0.285\textwidth} |}
   \hline
   \textbf{Date} & \textbf{Revision} & \textbf{Comments} & \textbf{Author(s)} \\ \hline
   Dec 29, 2017 & 1.0 & Main content done for all sections & Christopher McDonald \\ \hline
   Jan 1, 2018 & 1.1 & Edited document & Sharon Platkin \\ \hline
   Jan 3, 2018 & 1.2 & Edited document & Jared Rayner \\ \hline
   Mar 4, 2018 & 1.3 & Revised  Figures& Christopher McDonald \\ \hline
   Mar 5, 2018 & 1.4 & Edited scope & Sharon Platkin \\ \hline
   \end{tabularx}
   \caption{Revision History}
\end{figure}
\newpage
\section{Introduction}
\subsection{Project Overview}
SmartServe is an autonomous table tennis training system for table tennis players with various skill levels. SmartServe aids in diagnosing and improving a player's performance over time. The system trains table tennis players by shooting table tennis balls towards the player and detects successful returns from the player. The system can further adapt to the player's weaknesses and help them overcome it through further training. Importantly, SmartServe alleviates the problems of finding and working with a coach for players, as well as coaches trying to train multiple players simultaneously. The system will be deemed a success if the table tennis players and coaches can enjoy and see some value added by using SmartServe.\\ \\
The project started at the beginning of the Fall 2017 academic term and will conclude at the end of the Winter 2018 term. In addition, the core project team consists of final year Software and Mechatronics Engineering students who are enrolled in the MECHTRON 4TB6/SFWRENG 4G06 capstone project course.
\subsection{Document Overview}
This document will cover all potential hazards that a user may encounter when using the SmartServe system. For each hazard, a description, mitigation plan, and a fault tree to cover all potential situations in which the hazard would arise are included. Additionally, a description of the system, its scope, and boundary will be provided in order to support and provide context to the hazards. In addition to system hazards, project risks will also be considered where the hazards will place the successful completion of the project at risk. \\ \\
In order to complete this Hazard Analysis, a Fault Tree Analysis will be preformed. This will begin by identifying the hazards which exist in and around the system. From there, all causes for such hazard will be added into the tree. A cause could potentially have its own set of causes which make it happen and these will also be included in the fault trees until the root causes are identified.
\subsection{Naming Conventions and Terminology}
\label{sec:definitions}
The following terms and definitions will be used throughout this document:
\begin{itemize}
\item \textbf{ACID}: a database transaction which is atomic, consistent, isolated and durable
\item \textbf{CV}: computer vision
\item \textbf{FPS}: frames per second
\item \textbf{FSM}: finite state machine, shows transitions between states
\item \textbf{GUI}: graphical user interface
\item \textbf{IPO}: input process output
\item \textbf{ITTF}: International Table Tennis Federation
\item \textbf{Pitch}: rotation along the y-axis; this rotation angle primarily dictates the range of the ball from the net to the edge of the table on the user side
\item \textbf{Roll}: rotation along the x-axis
\item \textbf{Shooting Mechanism}: refers to the part of the system that shoots the table tennis balls towards the user side (player) Please refer to Figure \ref{fig:table-tennis-top-view} for visual illustration
\item \textbf{System}: encompasses both the hardware and software parts of SmartServe
\item \textbf{System Side}: the side of the table where the electromechanical system is placed; it is the opposite side of the User Side Please refer to Figure \ref{fig:table-tennis-top-view} for visual illustration
\item \textbf{TCP:} transmission control protocol
\item \textbf{Team}: all team members of the core capstone project, as noted in the list of Authors
\item \textbf{User Side}: the side of the table where the user (player) is standing
\item \textbf{Yaw}: rotation along the z-axis; this rotation angle primarily dictates the panning functionality of the shooting mechanism from the right side to the left side of the table
\end{itemize}

\begin{figure}[H]
   \centering
   
   \caption{Top View of the Tennis Table}
   \label{fig:table-tennis-top-view}
\end{figure}

\section{System}
\subsection{High-Level Design}
The high-level design document covers in great detail the design of the system and can be found \href{https://github.com/ChristopherMcDonald/SoftwareTronCapstone/blob/develop/documentation/SystemDesign/Design.pdf}{here}. As a summary, the mechanical aspects include a hopper to hold all the table tennis balls and a spinning disk with cut outs to force feed the balls into a barrel. The barrel can hold multiple balls, that are then pushed up the barrel as the aforementioned disk spins. Once a ball reaches the end of the barrel, the ball will be shot out via a spinning wheel affixed to a motor attached to the end of the barrel. The entire mechanism is fixed to a rotating platform to have variable yaw. The spinning wheel can shoot at various speeds and can be manually set to multiple orientations by rotating in the roll direction, to achieve different types of spin. The shooting assembly will also have multiple manual settings for rotating in the y-axis, in order to achieve different yaw and ball trajectories.  \\ \\
The electrical components include an Arduino, motors, a breadboard, a motor driver, an H bridge, and a power supply to control the motors needed to spin the mechanism and wheel. There will also be a general purpose computer to run the software-based components and a USB camera to use for the computer vision sub-system. 
\subsection{Scope \& Boundary}
The hazards outlined below will cover the hardware, electrical and software aspects of the SmartServe system. \\ \\
Intentional misuse or destruction of the system will not be discussed as it is outside the scope of this document. The user is assumed to be using fully-functioning and maintained equipment including the table tennis balls, table and paddles. 

\section{Hazards}
The hazards outlined here can be categorized into 2 main categories: system and project. System hazards damage the user or the assets of the system where project hazards damage the integrity of the project and its success. The list of each can be found in Table \ref{table:hazard}. \\
\begin{table}[H]
\centering
\caption{Categorization of Hazards}
\label{table:hazard}
\begin{tabular}{ | >{\raggedright\arraybackslash}p{0.5\textwidth} | >{\raggedright\arraybackslash}p{0.5\textwidth} | }
\hline
\multicolumn{2}{|c|}{\textbf{Hazards}} \\ \hline
\textbf{System}   & \textbf{Project}   \\ \hline
\begin{itemize}
\item User is struck by an air-borne ball
\item User is caught in a Pinch Point
\item Electric Shock
\item User's appendage is caught in machine
\item Machine overheats
\item Machine's traversal is blocked
\end{itemize}
&
\begin{itemize}
\item CV frame rate is too low for accurate reading
\item Shooting Mechanism shoots inaccurately
\end{itemize}
\\ \hline
\end{tabular}
\end{table}
\subsection{User is struck by an air-borne ball}
\subsubsection*{Description}
The machine will be shooting balls towards the user for them to return. For normal shots, it should always hit the table on the user side first before hitting a player. Not only is this a rule for valid shots as per the International Table Tennis Federation(ITTF) rules, it will ensure a sufficient amount of time for the user to react. However, the system could shoot the ball directly towards the player without hitting the table. This could potentially cause damage to the face or eyes of the player if the ball is traveling fast enough.
\subsubsection*{Mitigation Plan}
The system should never attempt to take a shot which exceeds the length of the user's side of the table. However, if a user were to replace the table with a smaller one without calibration or if some bug does make the spinning wheel spin faster than allowed, this could happen. The motor for the spinning wheel should have a maximum voltage in order to ensure the ball isn't shot at high speeds which would cause damage. \\ \\
The fault analysis tree can be found in Figure \ref{fig:ft-Air}.
\begin{figure}[H]
   \centering
    % requires the graphicx package
   \caption{Fault Analysis Tree for \textit{User is struck by an air-borne ball}}
   \label{fig:ft-Air}
\end{figure}

\subsection{User is caught in a Pinch Point}
\subsubsection*{Description}
The system will include moving mechanisms to shoot balls toward the player in a variety of ways. This means that two pieces could be moving next to one another. This may lead to a user's finger or other extremity being caught in between the two pieces. This can cause damage to the user and the system. The system can break the users skin or bones and the motors and materials can break if given enough force.
\subsubsection*{Mitigation Plan}
The number of pinch points should be minimized in order to avoid the chance of this happening. In the event one is unable to be avoided, proper notices and warnings will be used to discourage accidental exposure of the user's extremities to the pinch points. Additionally, guards will be installed wherever possible. \\ \\
The fault analysis tree can be found in Figure \ref{fig:ft-pinch}.

\begin{figure}[H]
   \centering
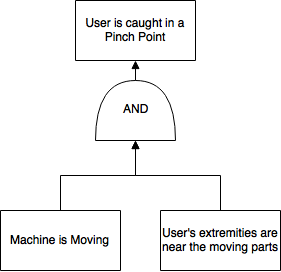
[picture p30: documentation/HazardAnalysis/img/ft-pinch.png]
    % requires the graphicx package
   \caption{Fault Analysis Tree for \textit{User is caught in a Pinch Point}}
   \label{fig:ft-pinch}
\end{figure}

\subsection{Electric Shock}
\subsubsection*{Description}
The system will require electrical components in order to activate motors. This will also include power balancing and transfer to the necessary components. This means some wiring will be needed and thus some inherent risk of shock to the user via such wiring or the sensors or actuators themselves. Only when the wires carry current would this be a risk.
\subsubsection*{Mitigation Plan}
All wiring will be enclosed to the best of our ability. However, due to the nature of the system requiring motion it can be difficult to completely enclose the system. Proper warnings and notices will be used to warn the user of electrical current. The system will also have a fail-safe via a fuse, which cuts power in the event of a short circuit. \\ \\

The fault analysis tree can be found in Figure \ref{fig:ft-electric}.

\begin{figure}[H]
   \centering
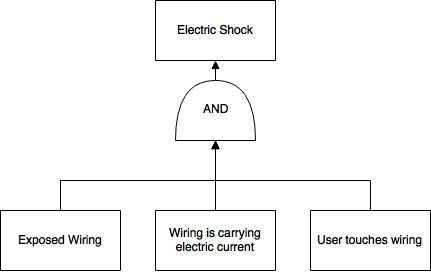
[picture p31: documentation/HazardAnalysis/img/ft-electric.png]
    % requires the graphicx package
   \caption{Fault Analysis Tree for \textit{Electric Shock}}
   \label{fig:ft-electric}
\end{figure}

\subsection{User's appendage is caught in machine}
\subsubsection*{Description}
Similar to a user's extremity, any loose appendages can also be of risk due to moving parts. An appendage could be a necklace, bracelet or any accessory. The risk goes up substantially for loose appendages. When the machine is moving, the appendage could get caught on or in between moving parts. When caught it could damage the appendage, the machine or the user.
\subsubsection*{Mitigation Plan}
The user must be warned not to wear such appendages when using this system. The number of points which would be vulnerable should be minimized. Similar to the extremity hazard, the locations which are vulnerable will be labelled appropriately and guarded. \\ \\

The fault analysis tree can be found in Figure \ref{fig:ft-appendage}.

\begin{figure}[H]
   \centering
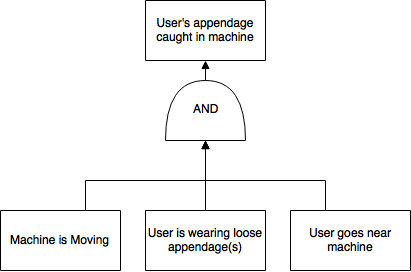
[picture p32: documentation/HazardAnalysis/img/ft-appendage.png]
    % requires the graphicx package
   \caption{Fault Analysis Tree for \textit{User's appendage is caught in machine}}
   \label{fig:ft-appendage}
\end{figure}

\subsection{Machine overheats}
\subsubsection*{Description}
The system is vulnerable to friction and overheating via electricity. This could cause mechanical failure where parts are damaged by this heat. It could also cause burns for a user who tries to handle the system when it overheats.
\subsubsection*{Mitigation Plan}
The system should shutdown after extreme prolonged use and is designed with appropriate fusing such that the power supply never exceeds electric load. \\ \\

The fault analysis tree can be found in Figure \ref{fig:ft-overheat}.

\begin{figure}[H]
   \centering
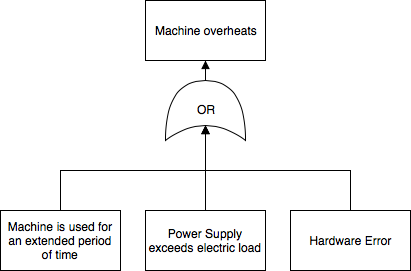
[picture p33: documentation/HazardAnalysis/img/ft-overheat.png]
    % requires the graphicx package
   \caption{Fault Analysis Tree for \textit{Machine overheats}}
   \label{fig:ft-overheat}
\end{figure}

\subsection{Machine's traversal is blocked}
\subsubsection*{Description}
As stated before, the system will contain moving parts to shoot in a variety of ways. A foreign object could be in the path which the system needs to travel. The system will attempt to travel this distance and if the foreign object isn't moved, either by the user or the machine itself, it could cause damage to the motors and mechanical parts of the system.
\subsubsection*{Mitigation Plan}
The user should ensure the system is clear of foreign objects within a certain radius of the machine and will be reminded to do so upon booting up the system. \\ \\

The fault analysis tree can be found in Figure \ref{fig:ft-traverse}.

\begin{figure}[H]
   \centering
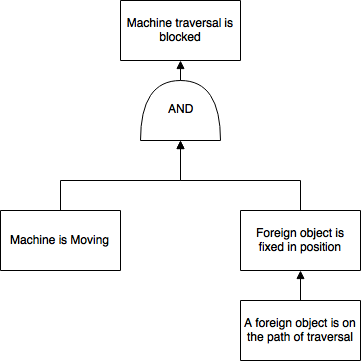
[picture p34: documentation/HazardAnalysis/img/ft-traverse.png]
    % requires the graphicx package
   \caption{Fault Analysis Tree for \textit{Machine's traversal is blocked}}
   \label{fig:ft-traverse}
\end{figure}

\subsection{CV frame rate is too low for accurate reading}
\subsubsection*{Description}
The table tennis ball will be tracked with computer vision as it travels across the system's side after being hit by the user. The speed at which it does this can vary from 1 to 30 m/s and the higher range can be difficult to track with consumer-grade hardware which includes cameras and processing power. If the ball travels too quickly, the hardware used for the system may read the ball's trajectory inaccurately.
\subsubsection*{Mitigation Plan}
To handle this risk, the following items will be considered. The hardware that the system uses can be improved to use higher frame rates or offer sufficent processing power to handle the images from the camera. The framework used for the computer vision may need to be edited, replaced or made entirely by the team to meet the performance demands. The camera may need to film at a higher frame rate and process the film later, causing a delay in feedback for the user. A physical mat on the system's side could be used to detect returns. \\ \\

The fault analysis tree can be found in Figure \ref{fig:ft-cv}.

\begin{figure}[H]
   \centering
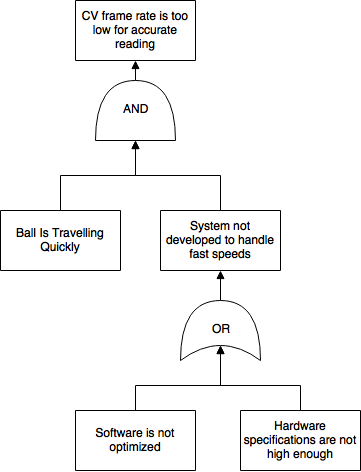
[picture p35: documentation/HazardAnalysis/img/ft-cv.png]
    % requires the graphicx package
   \caption{Fault Analysis Tree for \textit{CV frame rate is too low for accurate reading}}
   \label{fig:ft-cv}
\end{figure}

\subsection{Shooting Mechanism shoots inaccurately}
\subsubsection*{Description}
The Shooting Mechanism needs to spin a wheel to fire a ball at various degrees of pan which does introduce the possibility of inaccuracy when shooting the ball. If the wheel does not have the same contact with the ball for every shot, the speed, spin and position of the ball will vary between shots. If it does so too many times, it will not satisfy the requirements as set in the System Requirements document.
\subsubsection*{Mitigation Plan}
In order to reduce the severity and likelihood of this error, the following actions could be used. The first being buying better hardware which has more accurate specifications like motors and power supplies. The team could reduce the accuracy of the requirements, although this would endanger the user experience for the system. 

The fault analysis tree can be found in Figure \ref{fig:ft-shooting}.

\begin{figure}[H]
   \centering
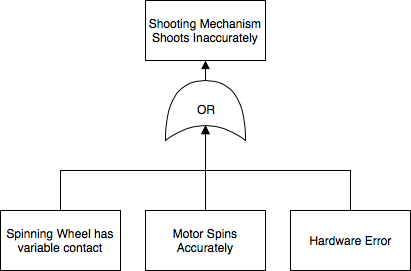
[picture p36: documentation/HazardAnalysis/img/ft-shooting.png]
    % requires the graphicx package
   \caption{Fault Analysis Tree for \textit{Shooting Mechanism shoots inaccurately}}
   \label{fig:ft-shooting}
\end{figure}

\end{document}

\subsection{}
\subsubsection*{Description}
\subsubsection*{Mitigation Plan}

The fault analysis tree can be found in Figure \ref{fig:ft-traverse}.

\begin{figure}[H]
   \centering
    % requires the graphicx package
   \caption{Fault Analysis Tree for \textit{Machine's traversal is blocked}}
   \label{fig:ft-traverse}
\end{figure}

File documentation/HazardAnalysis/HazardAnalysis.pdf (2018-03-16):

McMaster University

SmartServe

Software & Mechatronics Capstone

# Hazard Analysis

Authors:
Christopher McDonald - 001312456 Harit Patel - 001317372
Janak Patel - 001307060
Jared Rayner - 001311702
Nisarg Patel - 001322805
Sam Hamel - 001321692
Sharon Platkin - 001316625

Professor:
Dr. Alan Wassyng

Teaching Assistants:
Bennett Mackenzie
Nicholas Annable
Stephen Wynn-Williams
Viktor Smirnov

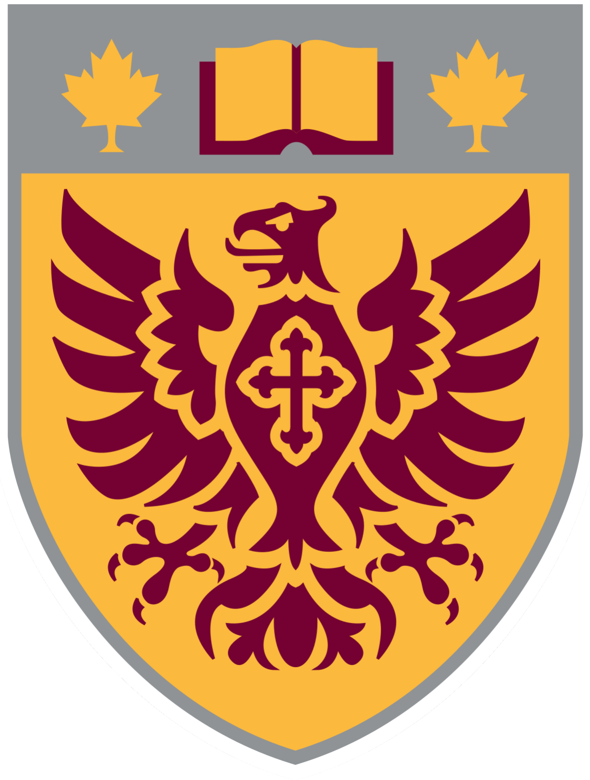
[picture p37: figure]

Last compiled on March 5, 2018

## Contents

1 Introduction | 3
1.1 Project Overview | | 3
1.2 Document Overview | | 3
1.3 Naming Conventions and Terminology | | 3
2 System | 5
2.1 High-Level Design | | 5
2.2 Scope & Boundary | | 6
3 Hazards | 6
3.1 User is struck by an air-borne ball | | 6
3.2 User is caught in a Pinch Point | | 7
3.3 Electric Shock | | 8
3.4 User’s appendage is caught in machine | | 9
3.5 Machine overheats | | 10
3.6 Machine’s traversal is blocked | | 11
3.7 CV frame rate is too low for accurate reading | | 12
3.8 Shooting Mechanism shoots inaccurately | | 14

## List of Figures

1 | Revision History | | 2
2 | Top View of the Tennis Table | | 5
3 | Fault Analysis Tree for User is struck by an air-borne ball | | 7
4 | Fault Analysis Tree for User is caught in a Pinch Point | | 8
5 | Fault Analysis Tree for Electric Shock | | 9
6 | Fault Analysis Tree for User’s appendage is caught in machine | | 10
7 | Fault Analysis Tree for Machine overheats | | 11
8 | Fault Analysis Tree for Machine’s traversal is blocked | | 12
9 | Fault Analysis Tree for CV frame rate is too low for accurate reading . . . . | 13
10 | Fault Analysis Tree for Shooting Mechanism shoots inaccurately | | 14

1

Date | Revision | Comments | Author(s)
Dec 29, 2017 | 1.0 | Main content done for all sections | Christopher McDonald
Jan 1, 2018 | 1.1 | Edited document | Sharon Platkin
Jan 3, 2018 | 1.2 | Edited document | Jared Rayner
Mar 4, 2018 | 1.3 | Revised Figures | Christopher McDonald
Mar 5, 2018 | 1.4 | Edited scope | Sharon Platkin

Figure 1: Revision History

2

## 1 Introduction

### 1.1 Project Overview

SmartServe is an autonomous table tennis training system for table tennis players with various skill levels. SmartServe aids in diagnosing and improving a player’s performance over time. The system trains table tennis players by shooting table tennis balls towards the player and detects successful returns from the player. The system can further adapt to the player’s weaknesses and help them overcome it through further training. Importantly, SmartServe alleviates the problems of finding and working with a coach for players, as well as coaches trying to train multiple players simultaneously. The system will be deemed a success if the table tennis players and coaches can enjoy and see some value added by using SmartServe.

The project started at the beginning of the Fall 2017 academic term and will conclude at the end of the Winter 2018 term. In addition, the core project team consists of final year Software and Mechatronics Engineering students who are enrolled in the MECHTRON 4TB6/SFWRENG 4G06 capstone project course.

### 1.2 Document Overview

This document will cover all potential hazards that a user may encounter when using the SmartServe system. For each hazard, a description, mitigation plan, and a fault tree to cover all potential situations in which the hazard would arise are included. Additionally, a description of the system, its scope, and boundary will be provided in order to support and provide context to the hazards. In addition to system hazards, project risks will also be considered where the hazards will place the successful completion of the project at risk.

In order to complete this Hazard Analysis, a Fault Tree Analysis will be preformed. This will begin by identifying the hazards which exist in and around the system. From there, all causes for such hazard will be added into the tree. A cause could potentially have its own set of causes which make it happen and these will also be included in the fault trees until the root causes are identified.

### 1.3 Naming Conventions and Terminology

The following terms and definitions will be used throughout this document:

- ACID: a database transaction which is atomic, consistent, isolated and durable
- CV: computer vision
- FPS: frames per second

3

- FSM: finite state machine, shows transitions between states
- GUI: graphical user interface
- IPO: input process output
- ITTF: International Table Tennis Federation
- Pitch: rotation along the y-axis; this rotation angle primarily dictates the range of the ball from the net to the edge of the table on the user side
- Roll: rotation along the x-axis
- Shooting Mechanism: refers to the part of the system that shoots the table tennis balls towards the user side (player) Please refer to Figure 2 for visual illustration
- System: encompasses both the hardware and software parts of SmartServe
- System Side: the side of the table where the electromechanical system is placed; it is the opposite side of the User Side Please refer to Figure 2 for visual illustration
- TCP: transmission control protocol
- Team: all team members of the core capstone project, as noted in the list of Authors
- User Side: the side of the table where the user (player) is standing
- Yaw: rotation along the z-axis; this rotation angle primarily dictates the panning functionality of the shooting mechanism from the right side to the left side of the table

4


Figure 2: Top View of the Tennis Table

## 2 System

### 2.1 High-Level Design

The high-level design document covers in great detail the design of the system and can be found here. (https://github.com/ChristopherMcDonald/SoftwareTronCapstone/blob/develop/documentation/SystemDesign/Design.pdf) As a summary, the mechanical aspects include a hopper to hold all the table tennis balls and a spinning disk with cut outs to force feed the balls into a barrel. The barrel can hold multiple balls, that are then pushed up the barrel as the aforementioned disk spins. Once a ball reaches the end of the barrel, the ball will be shot out via a spinning wheel affixed to a motor attached to the end of the barrel. The entire mechanism is fixed to a rotating platform to have variable yaw. The spinning wheel can shoot at various speeds and can be manually set to multiple orientations by rotating in the roll direction, to achieve different types of spin. The shooting assembly will also have multiple manual settings for rotating in the y-axis, in order to achieve different yaw and ball trajectories.

The electrical components include an Arduino, motors, a breadboard, a motor driver, an H bridge, and a power supply to control the motors needed to spin the mechanism and wheel. There will also be a general purpose computer to run the software-based components and a USB camera to use for the computer vision sub-system.

5

### 2.2 Scope & Boundary

The hazards outlined below will cover the hardware, electrical and software aspects of the SmartServe system.

Intentional misuse or destruction of the system will not be discussed as it is outside the scope of this document. The user is assumed to be using fully-functioning and maintained equipment including the table tennis balls, table and paddles.

## 3 Hazards

The hazards outlined here can be categorized into 2 main categories: system and project. System hazards damage the user or the assets of the system where project hazards damage the integrity of the project and its success. The list of each can be found in Table 1.

Table 1: Categorization of Hazards Hazards
System | Project
- User is struck by an air-borne ball • User is caught in a Pinch Point • Electric Shock • User’s appendage is caught in machine • Machine overheats • Machine’s traversal is blocked | • CV frame rate is too low for accurate reading • Shooting Mechanism shoots inaccurately

### 3.1 User is struck by an air-borne ball

Description

The machine will be shooting balls towards the user for them to return. For normal shots, it should always hit the table on the user side first before hitting a player. Not only is this a rule for valid shots as per the International Table Tennis Federation(ITTF) rules, it will ensure a sufficient amount of time for the user to react. However, the system could shoot

6

the ball directly towards the player without hitting the table. This could potentially cause damage to the face or eyes of the player if the ball is traveling fast enough.

Mitigation Plan

The system should never attempt to take a shot which exceeds the length of the user’s side of the table. However, if a user were to replace the table with a smaller one without calibration or if some bug does make the spinning wheel spin faster than allowed, this could happen. The motor for the spinning wheel should have a maximum voltage in order to ensure the ball isn’t shot at high speeds which would cause damage.

The fault analysis tree can be found in Figure 3.

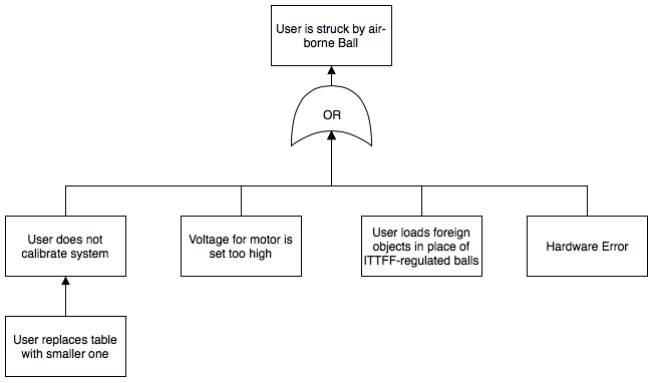
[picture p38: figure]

Figure 3: Fault Analysis Tree for User is struck by an air-borne ball

### 3.2 User is caught in a Pinch Point

Description

The system will include moving mechanisms to shoot balls toward the player in a variety of ways. This means that two pieces could be moving next to one another. This may lead to a user’s finger or other extremity being caught in between the two pieces. This can cause damage to the user and the system. The system can break the users skin or bones and the motors and materials can break if given enough force.

Mitigation Plan

The number of pinch points should be minimized in order to avoid the chance of this happening. In the event one is unable to be avoided, proper notices and warnings will be used

7

to discourage accidental exposure of the user’s extremities to the pinch points. Additionally, guards will be installed wherever possible.

The fault analysis tree can be found in Figure 4.

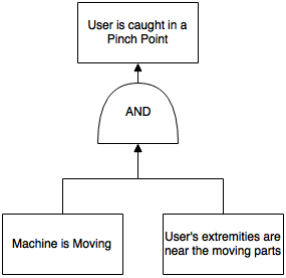
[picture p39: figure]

Figure 4: Fault Analysis Tree for User is caught in a Pinch Point

### 3.3 Electric Shock

Description

The system will require electrical components in order to activate motors. This will also include power balancing and transfer to the necessary components. This means some wiring will be needed and thus some inherent risk of shock to the user via such wiring or the sensors or actuators themselves. Only when the wires carry current would this be a risk.

8

Mitigation Plan

All wiring will be enclosed to the best of our ability. However, due to the nature of the system requiring motion it can be difficult to completely enclose the system. Proper warnings and notices will be used to warn the user of electrical current. The system will also have a fail-safe via a fuse, which cuts power in the event of a short circuit.

The fault analysis tree can be found in Figure 5.


Figure 5: Fault Analysis Tree for Electric Shock

### 3.4 User’s appendage is caught in machine

Description

Similar to a user’s extremity, any loose appendages can also be of risk due to moving parts. An appendage could be a necklace, bracelet or any accessory. The risk goes up substantially for loose appendages. When the machine is moving, the appendage could get caught on or in between moving parts. When caught it could damage the appendage, the machine or the user.

Mitigation Plan

The user must be warned not to wear such appendages when using this system. The number of points which would be vulnerable should be minimized. Similar to the extremity hazard, the locations which are vulnerable will be labelled appropriately and guarded.

9

The fault analysis tree can be found in Figure 6.

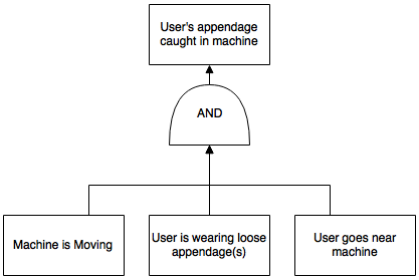
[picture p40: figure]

Figure 6: Fault Analysis Tree for User’s appendage is caught in machine

### 3.5 Machine overheats

Description

The system is vulnerable to friction and overheating via electricity. This could cause mechanical failure where parts are damaged by this heat. It could also cause burns for a user who tries to handle the system when it overheats.

Mitigation Plan

The system should shutdown after extreme prolonged use and is designed with appropriate fusing such that the power supply never exceeds electric load.

The fault analysis tree can be found in Figure 7.

10

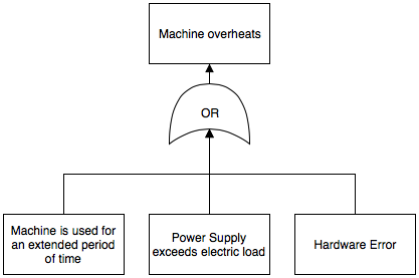
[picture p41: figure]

Figure 7: Fault Analysis Tree for Machine overheats

### 3.6 Machine’s traversal is blocked

Description

As stated before, the system will contain moving parts to shoot in a variety of ways. A foreign object could be in the path which the system needs to travel. The system will attempt to travel this distance and if the foreign object isn’t moved, either by the user or the machine itself, it could cause damage to the motors and mechanical parts of the system.

Mitigation Plan

The user should ensure the system is clear of foreign objects within a certain radius of the machine and will be reminded to do so upon booting up the system.

The fault analysis tree can be found in Figure 8.

11

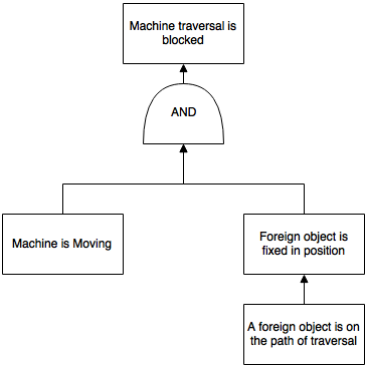
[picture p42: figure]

Figure 8: Fault Analysis Tree for Machine’s traversal is blocked

### 3.7 CV frame rate is too low for accurate reading

Description

The table tennis ball will be tracked with computer vision as it travels across the system’s side after being hit by the user. The speed at which it does this can vary from 1 to 30 m/s and the higher range can be difficult to track with consumer-grade hardware which includes cameras and processing power. If the ball travels too quickly, the hardware used for the system may read the ball’s trajectory inaccurately.

Mitigation Plan

To handle this risk, the following items will be considered. The hardware that the system uses can be improved to use higher frame rates or offer sufficent processing power to handle the images from the camera. The framework used for the computer vision may need to be edited, replaced or made entirely by the team to meet the performance demands. The camera may need to film at a higher frame rate and process the film later, causing a delay

12 in feedback for the user. A physical mat on the system’s side could be used to detect returns.

The fault analysis tree can be found in Figure 9.


Figure 9: Fault Analysis Tree for CV frame rate is too low for accurate reading

13

### 3.8 Shooting Mechanism shoots inaccurately

Description

The Shooting Mechanism needs to spin a wheel to fire a ball at various degrees of pan which does introduce the possibility of inaccuracy when shooting the ball. If the wheel does not have the same contact with the ball for every shot, the speed, spin and position of the ball will vary between shots. If it does so too many times, it will not satisfy the requirements as set in the System Requirements document.

Mitigation Plan

In order to reduce the severity and likelihood of this error, the following actions could be used. The first being buying better hardware which has more accurate specifications like motors and power supplies. The team could reduce the accuracy of the requirements, although this would endanger the user experience for the system.
The fault analysis tree can be found in Figure 10.

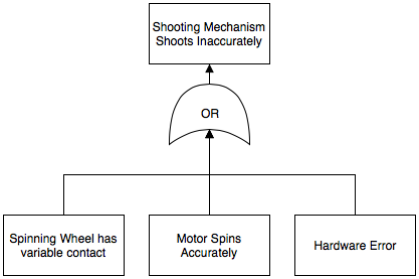
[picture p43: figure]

Figure 10: Fault Analysis Tree for Shooting Mechanism shoots inaccurately

14

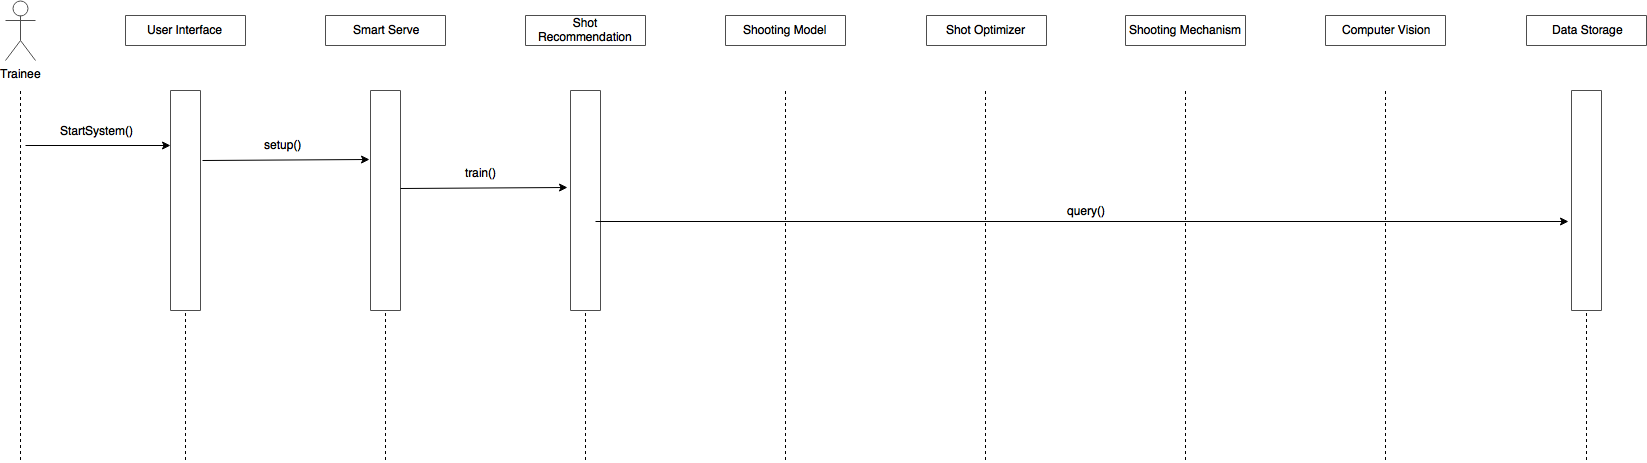
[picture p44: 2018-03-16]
documentation/HazardAnalysis/img/SequenceDiagram-Boot.png

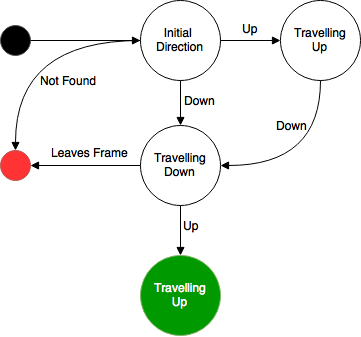
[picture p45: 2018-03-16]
documentation/HazardAnalysis/img/cvFSM.png

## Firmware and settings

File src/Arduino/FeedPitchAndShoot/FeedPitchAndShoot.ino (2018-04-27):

#include <FeedAndShoot.h>
#include <Pitch.h>
#define Steps_For_1_REV 515

Pitch* mypitch;
FeedAndShoot* myfeedandshoot;
String data;

void setup() 
{
    mypitch = new Pitch();
    myfeedandshoot = new FeedAndShoot();
    mypitch->home_assembly();
    // make sure this matches one in Java
    Serial.begin(9600);
    myfeedandshoot->set_dcspeed(0);
    Serial.write('A');
}

void loop() {
    if (Serial.available() > 0) {                      // if data has been written to the Serial stream
        data = Serial.readString();                     // strings are in form "P:45.0"

        int sep = data.indexOf(':');
        String type = data.substring(0, sep);           // returns "45.0"
        double val = data.substring(sep + 1).toDouble();// converts ^ to Double

        if(type == "V") {
            myfeedandshoot->set_dcspeed(val);
        } 
        else if (type == "S")
        {
        	myfeedandshoot->stop_feed_shot();
        	mypitch->stop_pitch();
        }
        else 
        { // type == "P"
            delay(1000);
            mypitch->move_respect_to_horizon(val);
            myfeedandshoot->move_by_steps(Steps_For_1_REV);
        }
    }
}

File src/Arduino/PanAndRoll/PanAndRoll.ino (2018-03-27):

#include <AutomaticPanning.h>
#include <AutomaticRoll.h>

AutomaticPanning* myautopan = new AutomaticPanning();
AutomaticRoll* myautoroll = new AutomaticRoll();

String data;        //variable to store incoming data from JAVA

void setup() {
    // make sure this matches one in Java
    Serial.begin(19200);
    myautoroll->home_assembly("CCW");
    myautopan->home_assembly("CW");
}

void loop() {
    // pan values from 0 to 180
    // roll 0, 45, 135

    if(Serial.available() > 0) {                  // if data has been written to the Serial stream
        data = Serial.readString();               // strings are in form "45.0,45.0"

        int comma1 = data.indexOf(',');
        String val1 = data.substring(0, comma1);  // returns "45.0"
        double pan = val1.toDouble();             // convert ^ to Double

        data = data.substring(comma1 + 1);        // strip first value and comma
        double roll = data.toDouble();            // convert ^ to Double

        if(!(myautopan->move_to_location(pan))) { // pans first
            Serial.write('C');                      // "not done" flag
        } else {
            if(!(myautoroll->move_to_location(roll))) { // then rolls
                Serial.write('C');
            } else {
                Serial.write('B');                    // "done" flag
            }
        }
    }
}

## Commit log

2017-11-28 Prototyping process flow revised
2017-11-28 Revised rapid prototype diag. + trello
2017-12-30 Added Bread board, schematic and pcb diagram
2017-12-30 Created a Table model, to be reviewed for Janak and Jared
    [Table Tennis Table.prt]
2017-12-30 Designed Inner PVC pipe with 10cm, 15cm and 20 cm length and with 3D printer files
    [Inner_PVC_Tube_Prototype.prt, Inner_PVC_Tube_Prototype.stl, Inner_PVC_Tube_Prototype_15cm.stl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]
2017-12-30 Added a 3D model of the shaft adapter for Automatic Feeder along with STL file for 3D Printing
    [Shaft Adapter for Automatic Feeder.prt, Shaft Adapter for Automatic Feeder.stl]
2017-12-30 moved folder
    [Inner_PVC_Tube_Prototype.prt, Inner_PVC_Tube_Prototype.stl, Inner_PVC_Tube_Prototype_15cm.stl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]
2018-01-08 Merge branch 'master' of https://github.com/ChristopherMcDonald/SoftwareTronCapstone
    Reworded and added some material to high level design. Fixed spelling mistakes in user strck by airborn ball and user caught in pinch point. Added hazard of user not communicating current pitch and roll settings properly. Added ft-settings.png to support harzard.
2018-01-17 Added Janak & Jared's Design plus created a 3D Print Files folder
    [Feeder Cutout.prt, Inner_PVC_Tube_Prototype.stl, Inner_PVC_Tube_Prototype_15cm.stl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]
2018-02-01 added arduino stuff
2018-02-01 working for detecting 100 frames
2018-02-01 sql connector
2018-02-01 arduino working
2018-02-01 Added a automatic_panning_tester that contains all of the class testing and header testing sample instruction that can be tested
2018-02-01 Corrected Proof Of Concept code from merging problem
    [FeedAndShoot.cpp]
2018-02-01 DC motor class stuff working perfect
2018-02-01 Working on the servo for the feeder
2018-02-01 threading working
2018-02-01 UI buttons
2018-02-01 replaced controller with threaded one
2018-02-13 some process stuff
    [data-f.csv, data-nf.csv]
2018-02-17 edits across the board
2018-02-18 finalized testing
    [data-f.csv, data-nf.csv]
2018-02-25 forgot something
    [data-f.csv, data-nf.csv]
2018-03-19 added dc motor specs
2018-03-19 added stepper specs
2018-03-19 switched out degree impl
2018-03-19 added trace matrix
2018-03-23 Need to Test Automatic Roll with the H/W and Arduino, next step make header files for servo motor of pitch
2018-03-23 Header files Compilation tested along with Pitch testing code added
2018-03-23 changed pin to 12
2018-03-23 Recalibrated home position to 70.0 deg and changed the pin to # 12
2018-04-01 buttons pressed
2018-04-04 toggle buttons
2018-04-27 added pitch and made ui for testing
2018-04-27 internal frame
2018-04-27 graph-chart switch needs fixing
2018-04-27 Increased the diameter of the Feeder Cutout to possibly fix the jam error
    [Feeder Cutout.prt]
2018-04-27 Modified Pitch.cpp such that the HOME is at 60 degrees, added Integration Test file for Arduino
2018-04-27 Reverted the Feeder Cutout to original 110 mm diameter, after removing the stopper
    [Feeder Cutout.prt]
2018-04-27 Corrected Pitch header files to not go below 0 degrees, added step by step execution so there are no jerks during movement
    [Pitch.cpp]
2018-04-27 Allowed Pitch library to print
2018-04-27 Added gradual slow down for the DC motor
